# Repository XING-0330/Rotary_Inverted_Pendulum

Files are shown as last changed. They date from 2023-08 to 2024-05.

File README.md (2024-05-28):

Project_1 旋轉倒單擺
===
成果影片: [https://youtube.com/shorts/ecyUvNsTMwk](https://youtu.be/7YaTq_cNlhs)

介紹
---
**旋轉倒單擺(Rotary Inverted Pendulum)** 是一個經典的控制問題，結合了旋轉運動和單擺運動，相當於雙級的直線倒單擺。其特點是一個懸掛的棒狀物體，可以在一個固定點進行旋轉運動，同時在這個棒的另一端懸掛一個單擺。這種運動展示了複雜的動力學行為，廣泛應用於物理學教育和研究。

3D 模型建構 & 實際模型搭建
---
### 模型
本人使用 **Fusion360** 進行 3D 模型繪製，如下圖所示:

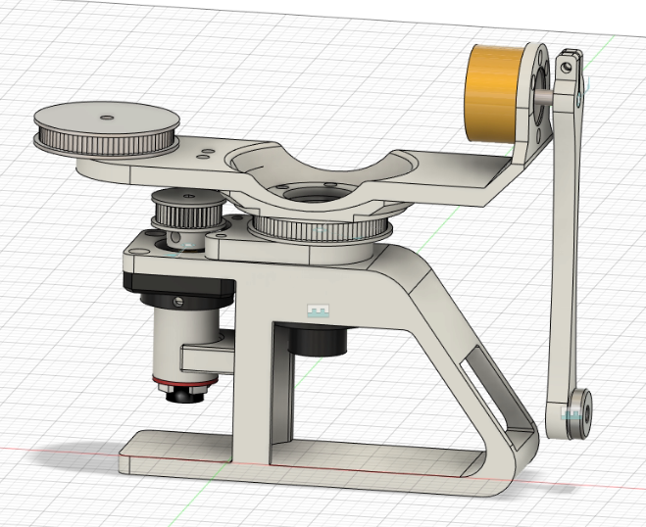
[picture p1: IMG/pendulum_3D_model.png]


透過左下方的馬達利用皮帶帶動搖臂進行旋轉，進而帶動右方單擺甩起。在左上方有加了一個和編碼器差不多重量的金屬同步輪作為配重，經過測試證實可以有效降低旋轉時的慣性。

### 電路
使用 arduino mega 2560 搭配 TB6612FNG 直流馬達驅動版進行控制
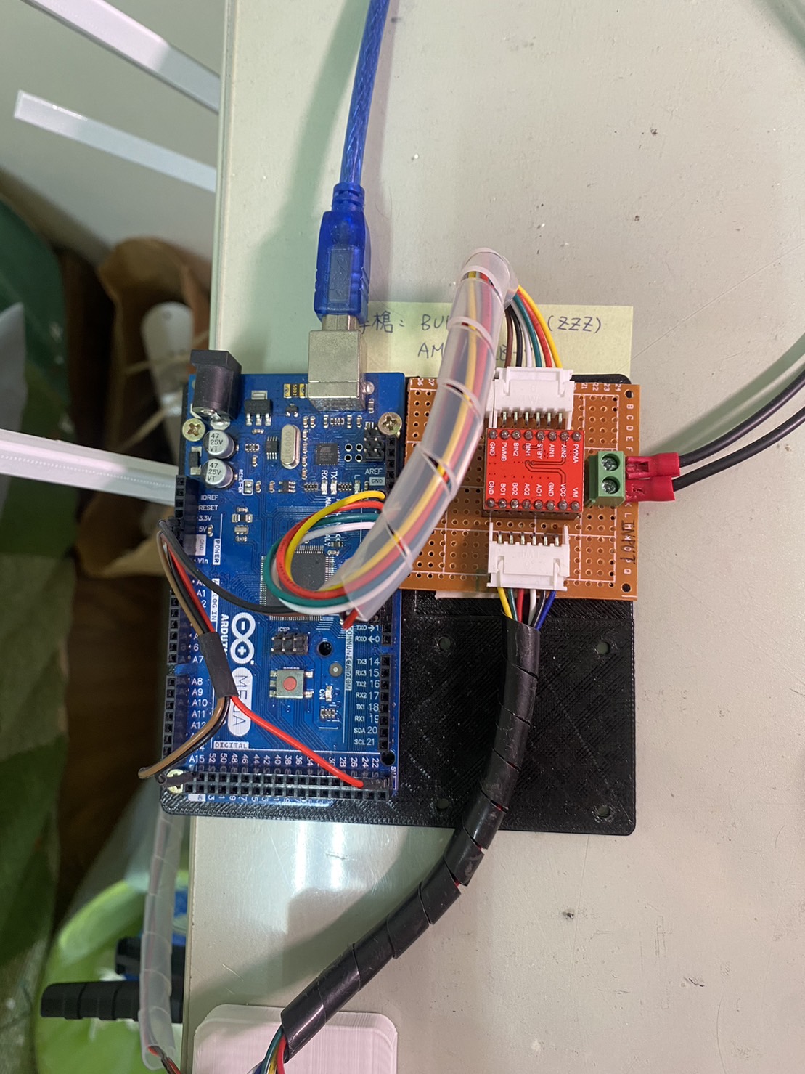
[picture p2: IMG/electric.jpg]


### 組裝
所繪製的模型和其他零件及電路部分皆可在 `Hardware` 中找到，最終組裝後的結果如下:

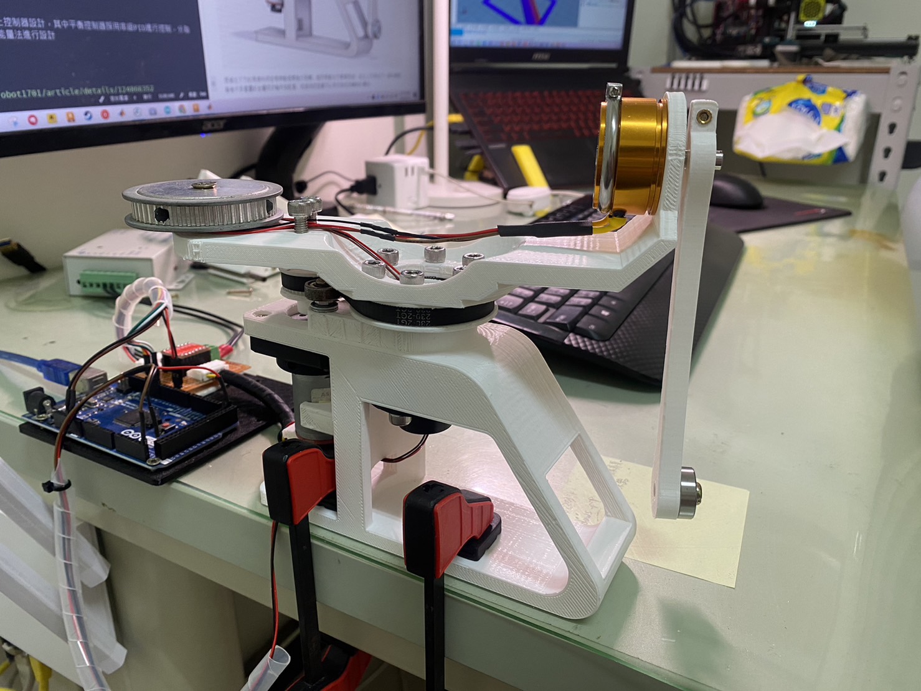
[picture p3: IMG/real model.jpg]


>自己覺得比較要注意的零件是編碼器和下方的旋轉盤，上方角度建議使用絕對式編碼器，而下方馬達所使用的則是推薦使用增量式編碼器，而下方旋轉盤是為了防止線會捲在一起。

運動學分析
---
我們可透過拉格朗日方程式去進行求解
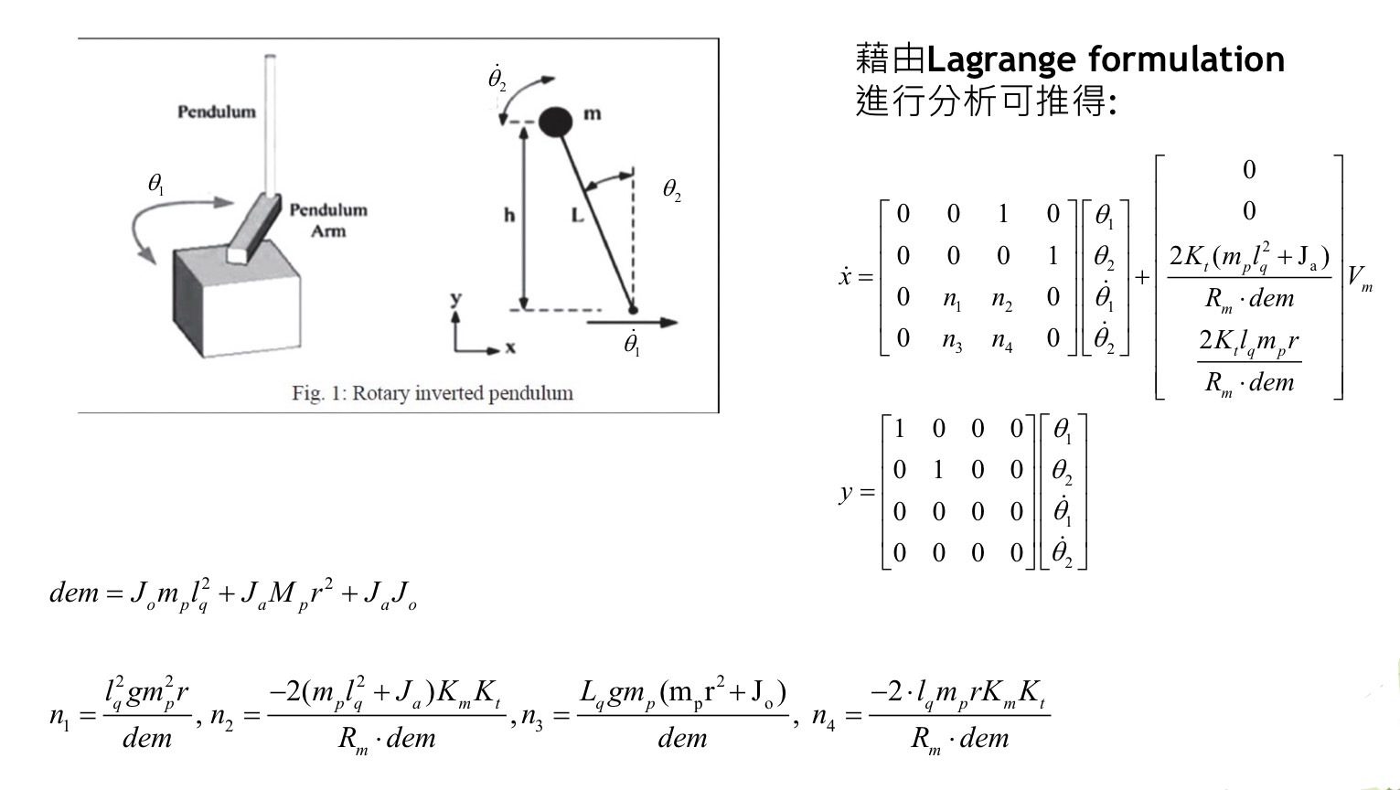
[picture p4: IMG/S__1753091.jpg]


Matlab 模擬
---
將上述所繪製之3D圖檔轉成 simscape 去進行模擬，詳細步驟可[參考以下影片][1]

[1]:<https://www.youtube.com/watch?v=pDiwAA1cnb0&t=0s>

有了 simscape 讓我們可以很方便的進行控制器的設計。

程式撰寫
---
### 控制器設計

我們將控制器分為平衡控制器、甩上控制器設計，其中平衡控制器採用串級PID進行控制，分為角度環和位置環，而甩上則是透過能量法進行設計。

* 平衡控制器
    
    角度環控制的是單擺是否立直，而位置環是要讓單擺穩定在一個特定角度。要是沒有位置環只有角度環，單擺會一直朝一個方向旋轉。

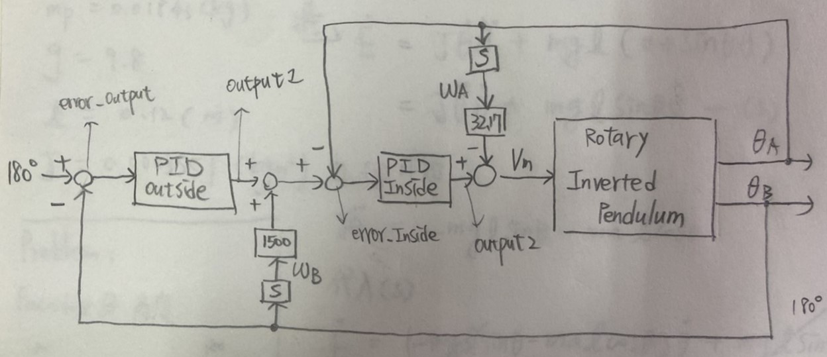
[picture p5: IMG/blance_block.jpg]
    

* 甩上控制器
    
    開始給擺桿一個速度，隨後擺桿會擺會到𝜃=0，但是速度不為0，此時給倒立擺一個與擺桿運動方向相反的速度，之後擺桿狀態為a<0,𝜃<0；等再次𝜃=0時，速度不為0，此時再次給倒立擺一個與擺桿運動方向相反的速度，之後會重複a>0,𝜃<0;a<0,𝜃>0;這兩個狀態，倒立擺能量就會積攢，最後達到目標位置附近。

**反向速度計算公式**
  
$$\begin{align\*}
V_{swing}=K(E-E_{target})\times sign(\omega_Bcos(\theta_B))
\end{align\*}$$

**積攢能量計算公式**
  
$$\begin{align\*}
&E=\frac{1}{2}J{\omega_{B}}^{2}+mgH\\\\\\
&E_{target}=2mgl\\\\\\
&H=l(1-cos(\theta_B))\\\\\\
&\theta_B=\text{pendulum angle}
\end{align\*}$$

### 整體架構

根據單擺的角度去切換使用平衡控制器及甩上控制器，整體控制方塊圖如下

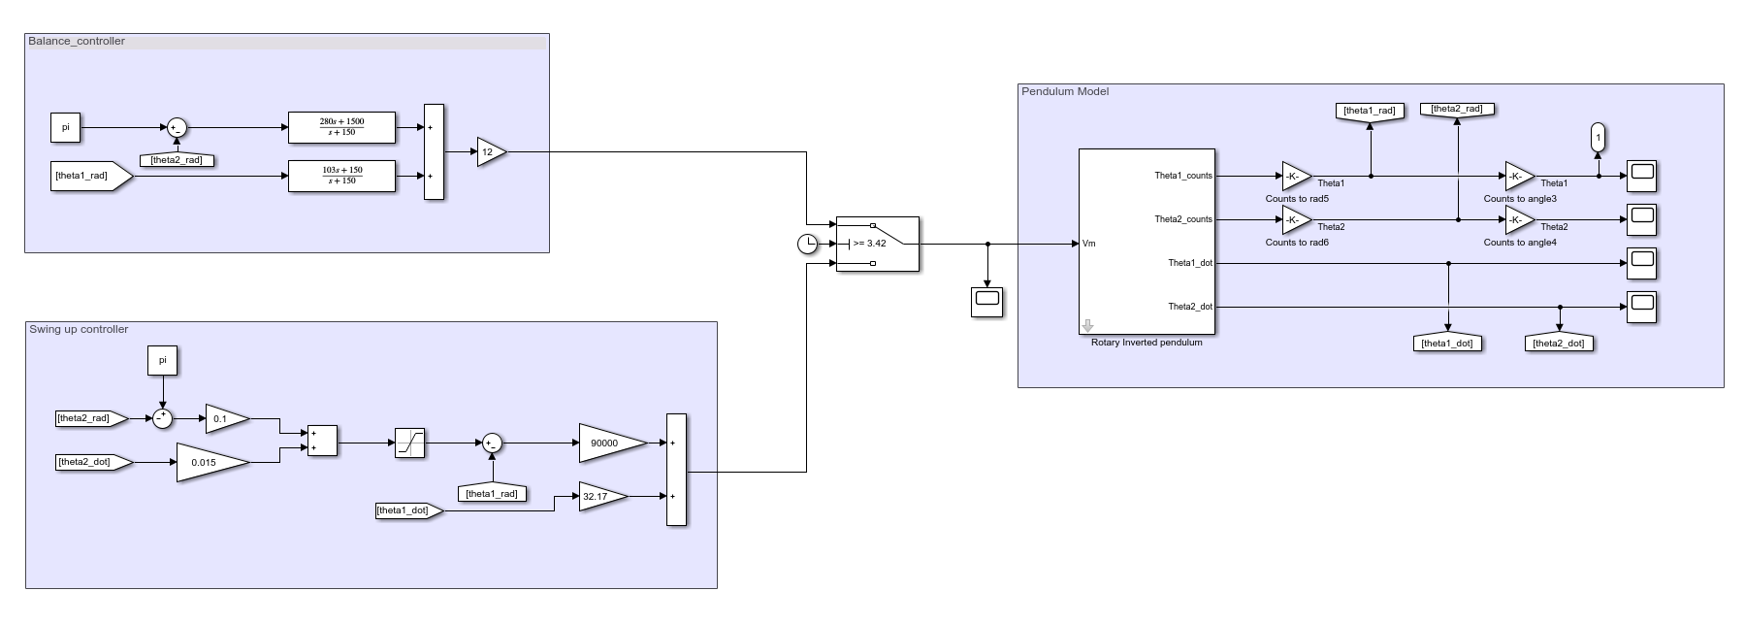
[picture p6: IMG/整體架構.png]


參考資料
---
1. 甩上控制 
https://blog.csdn.net/robot1701/article/details/124866352
2. 參數調整 
https://blog.csdn.net/a568713197/article/details/91600285 https://blog.csdn.net/small_po_kid/article/details/107659413
3. PID 程式撰寫
https://github.com/ToanTech/DengFOC_Lib/blob/main/DengFOC%20%E5%BA%93/V0.2/DengFOC.cpp
4. TB6612 直流馬達控制板
https://swf.com.tw/?p=1066
5. 倒立擺控制論文
Nath, K., & Dewan, L. (2018, March). Heuristic optimization based choice of LQR weighting matrices for a rotary inverted pendulum. In 2018 International Conference on Recent Trends in Electrical, Control and Communication (RTECC) (pp. 269-274). IEEE.

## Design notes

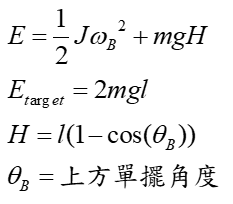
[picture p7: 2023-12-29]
IMG/formula2.png

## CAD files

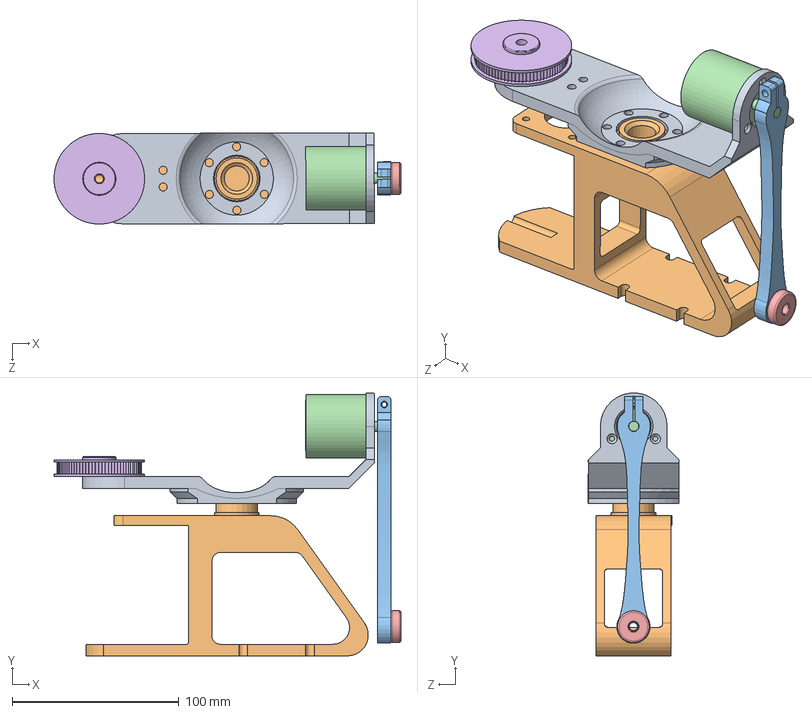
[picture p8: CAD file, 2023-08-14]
Matlab_simulation/RotaryInvertedPendulum.SLDASM
207.8 x 157.5 x 54.6 mm
MyArm
MyBottom
pendulum
Encoder
bearing
synchronous wheel

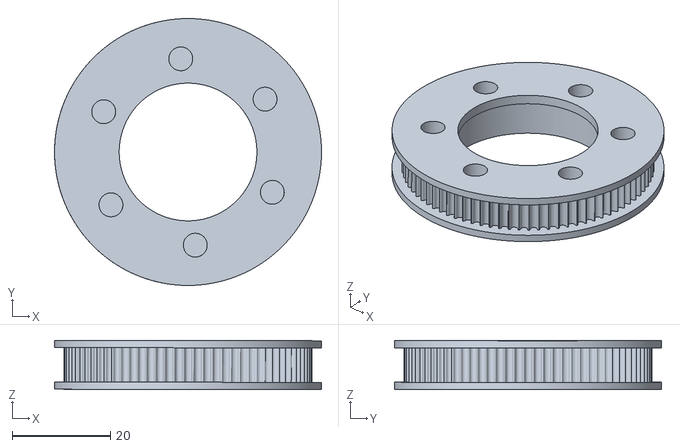
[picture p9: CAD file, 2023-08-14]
Hardware/Stl/Synchronous_wheel_2GT_80T .stl
54.3 x 54.3 x 10.0

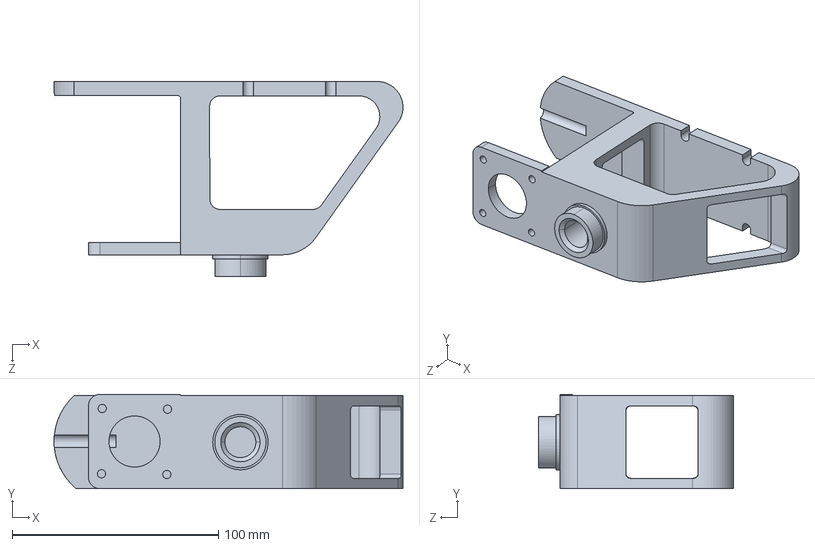
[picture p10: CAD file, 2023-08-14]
Matlab_simulation/MyBottom_預設_sldprt.STEP
169.2 x 45.6 x 94.5 mm

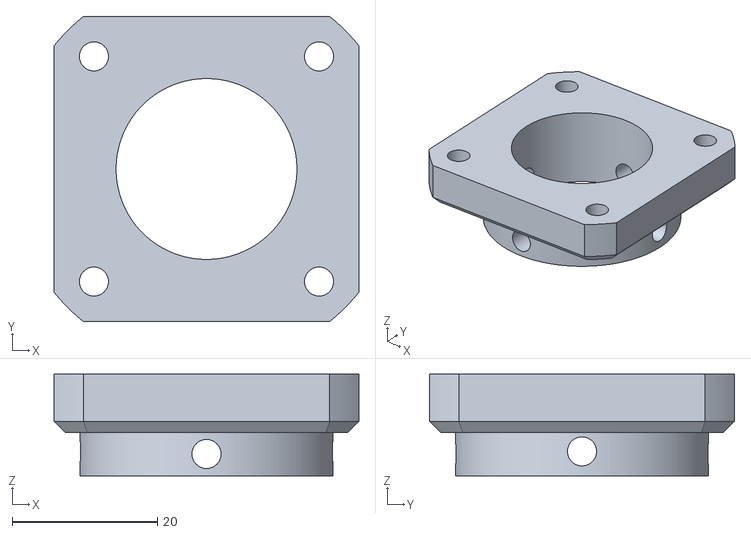
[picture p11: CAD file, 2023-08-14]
Hardware/Stl/motor_holder.stl
42.0 x 42.0 x 14.0

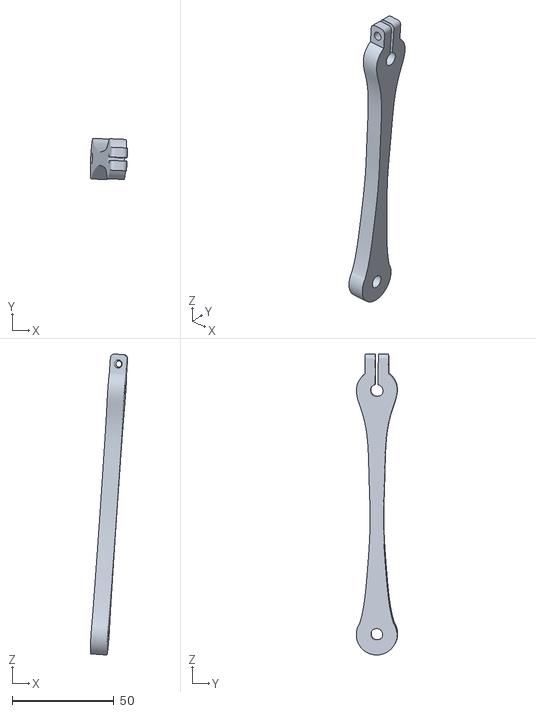
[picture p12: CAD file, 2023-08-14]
Hardware/Stl/pendulum.stl
18.3 x 20.3 x 147.9

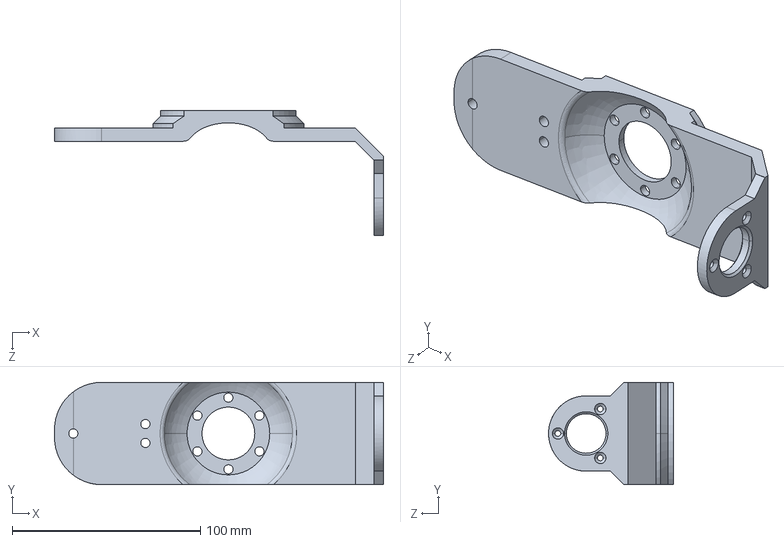
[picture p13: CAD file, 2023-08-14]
Matlab_simulation/MyArm_預設_sldprt.STEP
174.7 x 54.3 x 66.3 mm

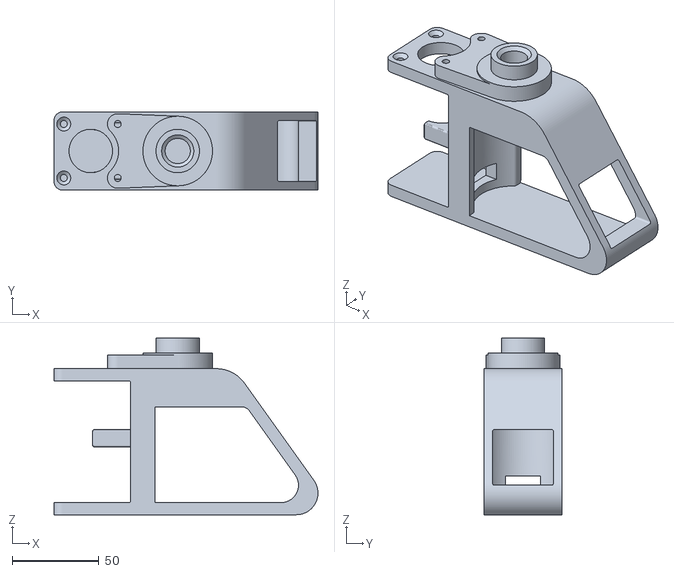
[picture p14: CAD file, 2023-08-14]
Hardware/Stl/pendulum_bottom.stl
151.8 x 45.0 x 101.5

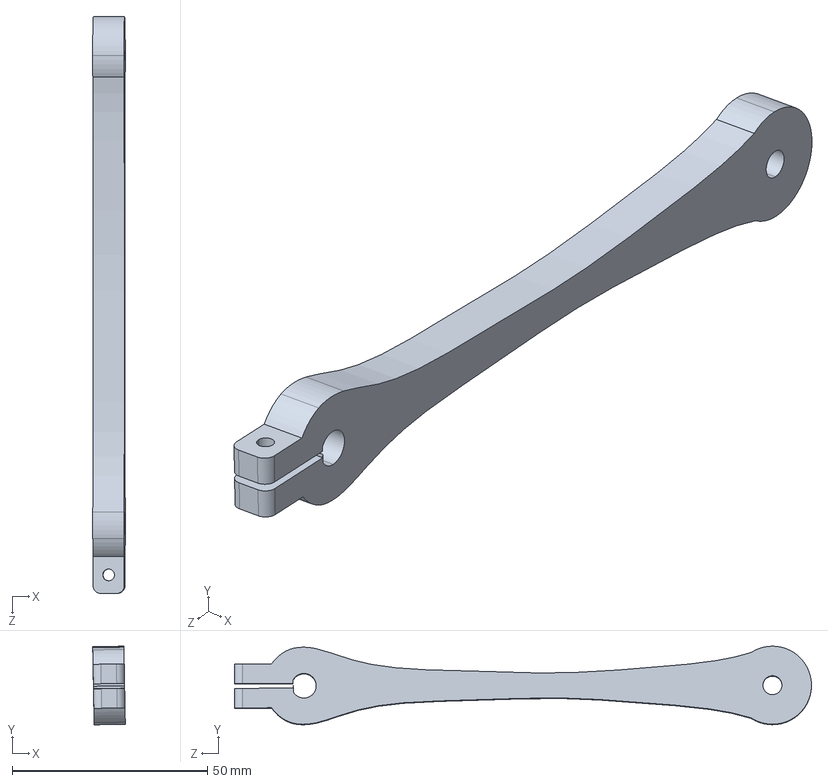
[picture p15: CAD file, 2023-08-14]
Matlab_simulation/pendulum_預設_sldprt.STEP
8.38 x 20.2 x 147.8 mm

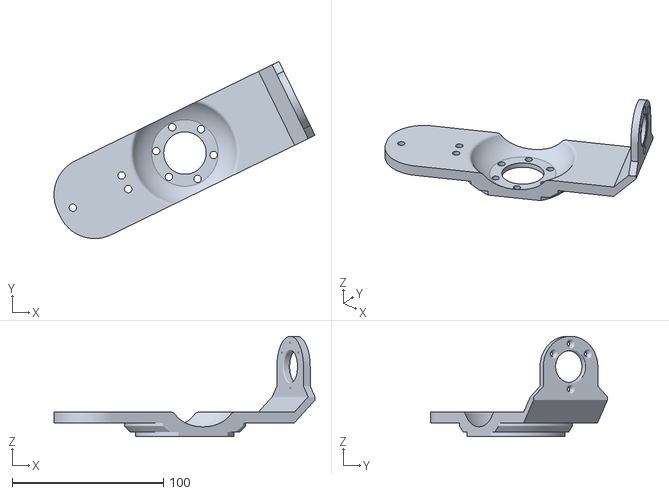
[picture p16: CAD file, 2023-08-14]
Hardware/Stl/Arm.stl
172.4 x 116.9 x 66.3

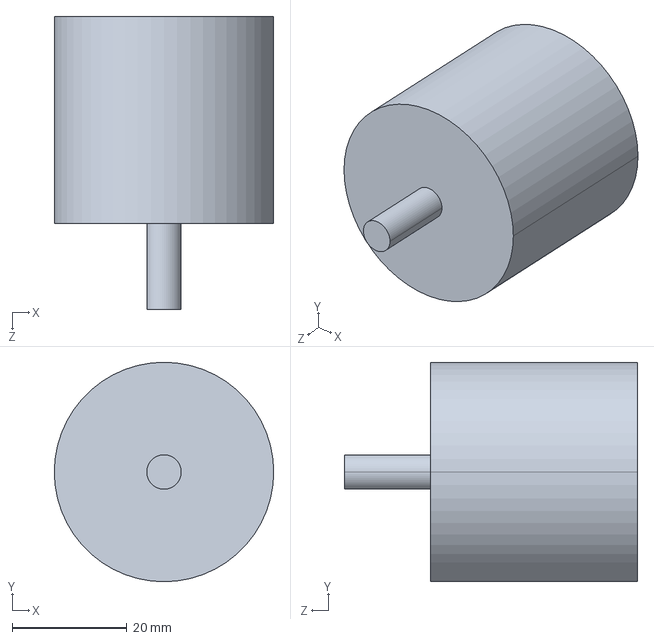
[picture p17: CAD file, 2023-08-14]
Matlab_simulation/Encoder_預設_sldprt.STEP
38.2 x 38.2 x 51.0 mm

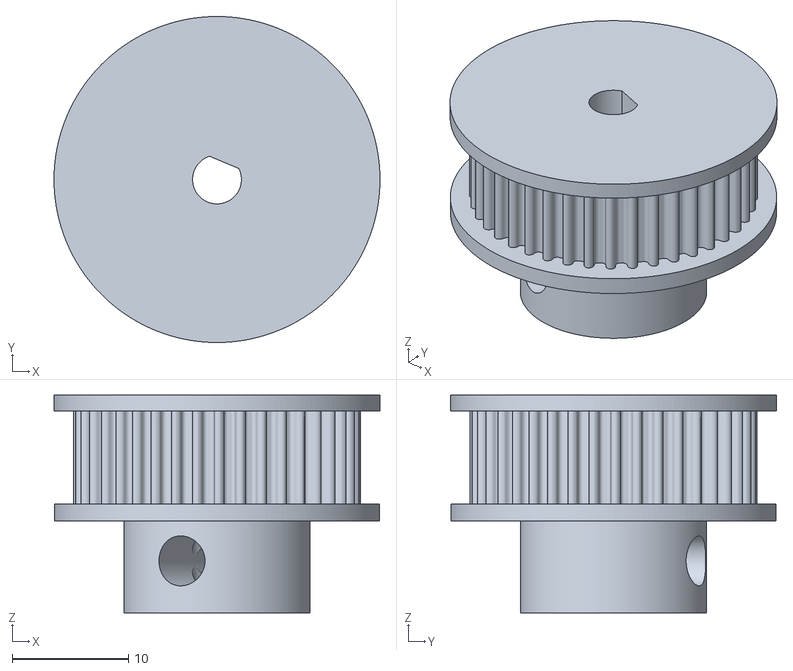
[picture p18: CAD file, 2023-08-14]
Hardware/Stl/Synchronous_wheel_2GT_40T.stl
28.1 x 28.1 x 18.8

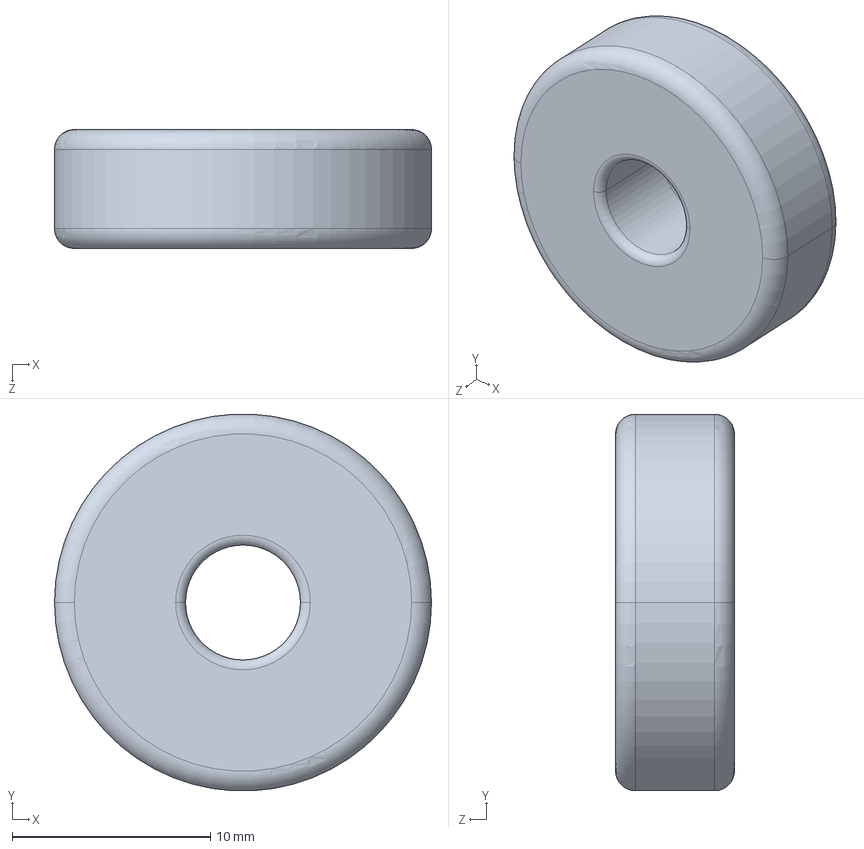
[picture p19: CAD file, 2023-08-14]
Matlab_simulation/bearing_預設_sldprt.STEP
19.0 x 19.0 x 6.00 mm

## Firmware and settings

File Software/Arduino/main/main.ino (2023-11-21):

// Include library 
#include <SparkFun_TB6612.h>
#include "pid.h"
#include "lowpass_filter.h"

// Mechanical parameter
float J = 0.0004;
float m = 0.02;
float g = 9.8;
float l = 0.12; 

// Motor_A
#define ENCODER_A_PIN 2 
#define ENCODER_B_PIN 3
#define ENC_COUNT_REV 97

float pulse_A = 0;
float theta_A = 0;
float pre_theta_A = 0;
float pre_1500_theta_A = 0;
float omega_A = 0;

long previousMillis_A = 0;
long currentMillis_A = 0;

Motor motorA = Motor(10, 9, 11, 1, 8);

// Motor_B
int theta_B = 0;
int pre_theta_B = 0;
int theta_B_V2 = 0;
float theta_B_V2_rad = 0;

float omega_B = 0;
float omega_B_rad = 0;
long previousMillis_B = 0;
long currentMillis_B = 0;

// PID
PIDController pid_outside = PIDController{42, 0, 96, 10000.0, 255.0};
PIDController pid_inside = PIDController{0.385, 0.0, 1.707, 1000.0, 255.0};

// Other
int t = 0;
int num = 0;
int interval = 20;
float delta = float(interval)/1000;
int count_output;
float error_Outside = 0;
float error_Inside = 0;
float output_1 = 0;
float output_2 = 0;
int VM_pwm = 0;
float Position_target = 0;
float Energy_target = 2*m*g*l*100;
float Energy = 0; 

float SW_pwm = 0;

LowPassFilter LPF = LowPassFilter(0.01);
 
/* ===================================================================================== */
void setup() {
  Serial.begin(115200);
  
  // Motor_A
  pinMode(ENCODER_A_PIN, INPUT_PULLUP);
  pinMode(ENCODER_B_PIN, INPUT_PULLUP);
  attachInterrupt(digitalPinToInterrupt(ENCODER_A_PIN), interrupt_change_A, CHANGE);
  
  // Motor_B
  pinMode(A15, INPUT);
}

void loop() 
{
  t = micros()/1.0e3;
  routine(); 

// Swing up Controller
  swing_up(32);
  SW_pwm = constrain(SW_pwm, -255, 255);
  
  if(abs(theta_B_V2) < 14)
  {
    motorA.drive(SW_pwm,1);
  }
 
// Balance Controller
  if(theta_B > 170 && theta_B < 190)
  {
    if((t%30 == 0)) output_2 = Circle_position(Position_target);
    else if(t%5 == 0)
    {
      output_1 = Circle_angle(180);
      VM_pwm = output_1 - output_2;  
      motorA.drive(VM_pwm,1);
    } 
  }

  // Safety setting
  if(abs(theta_A) > 600)
  {
    motorA.brake();
    pulse_A = 0; 
  }
  
  Print();
  
}
// function 
/* ===================================================================================== */
void routine(){
  angle_A();
  angle_B();
  speed_calculate_B();

  Energy_calculate();
}

/* Angle calculate */
// Motor_A
void interrupt_change_A(){

  (digitalRead(ENCODER_A_PIN) == digitalRead(ENCODER_B_PIN)) ? --pulse_A : ++pulse_A;
  angle_A();
}

void angle_A(){
  // degree
  theta_A = (pulse_A*360/97)*0.5;
}

void speed_calculate_A() {

  currentMillis_A = millis();
 
  if (currentMillis_A - previousMillis_A > interval) {
 
    previousMillis_A = currentMillis_A;
    
    omega_A = (float)( (theta_A - pre_theta_A)/delta );
    
    pre_theta_A = theta_A;
   
  }
}

// Motor_B
void angle_B(){
  // degree - V1 (0 - 90 - 180 - 270 - 360)
  theta_B = map(analogRead(A15),0,1023,0,359);
  
  // degree - V2 (+180 - +90 - 0 - (-90) - (-180))
  if(theta_B > 180 && theta_B < 360)(theta_B_V2 = theta_B - 360);
  else if(theta_B >= 0 && theta_B <= 180)(theta_B_V2 = theta_B);
  theta_B_V2_rad = (float)(theta_B_V2)*3.14/180; 
}

void speed_calculate_B() {  // speed calculate must according to theta_B_V2 ,because value must continue

  currentMillis_B = millis();
 
  if (currentMillis_B - previousMillis_B > interval) {
 
    previousMillis_B = currentMillis_B;
    
    omega_B = (float)( (theta_B_V2 - pre_theta_B)/delta );

    omega_B_rad = omega_B*3.14/180;
    
    pre_theta_B = theta_B_V2;
   
  }
}

/* Banlance ontroller design */
// Angle_LOOP
float Circle_angle(int Target_1)
{
  error_Outside = (Target_1 - theta_B); 
  output_1 = pid_outside(error_Outside);
  return output_1; 
}

// Position_LOOP
float Circle_position(int Target_2)
{
  error_Inside = (Target_2 - theta_A);
  output_2 = pid_inside(error_Inside);
  output_2 = LPF(output_2);
  return output_2;
}

/* Swing up ontroller design */
// Energy
void Energy_calculate()
{
  float H = l*(1 - cos(theta_B_V2_rad)); 
  Energy = 0.5*J*pow(omega_B_rad, 2) + m*g*H;
  Energy = 100*Energy;
}
// Swing up
void swing_up(float Ke)
{
  SW_pwm = Ke*(Energy - Energy_target)*sign(omega_B_rad*cos(theta_B_V2_rad));
}

float sign(float x)
{
  if(x>1)x = 1;
  else if(x<-1)x = -1;
  return x;
}

/* Output */
// Print ( loop 20 times print ince )
void Print(){
  count_output++;
  if(count_output >= 20)
  {
    count_output = 0;
    
    Serial.print(theta_A);
    Serial.print("\t");
    Serial.print(theta_B);
    Serial.print("\t");
    Serial.print(theta_B_V2);
    Serial.print("\t");
    Serial.println(theta_B_V2_rad);
  }
}

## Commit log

2023-08-14 Add Hardware file and matlab simulation file
    [Arm.stl, BOM.xlsx, Encoder_預設_sldprt.STEP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]
2023-11-21 Simplify the calculation process
    Using ternary operator to reduce the temporary variable and refine the code
    in interrupt.
